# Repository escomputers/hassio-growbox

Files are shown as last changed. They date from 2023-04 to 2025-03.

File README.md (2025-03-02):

Home Assistant as growbox controller, using several different devices and sensors, connected via D1 Mini/ESP8266-12-e

## Home Assistant setup

### Install
1. Install Home Assistant as container (for Core installation check the "core" branch out)

```bash
docker compose up -d
```

2. Connect esp8266 to your PC using USB cable (buy one with serial converter integrated) and install ESPHome Device builder:

- https://esphome.io/guides/getting_started_command_line#bonus-esphome-device-builder
- https://esphome.io/guides/getting_started_hassio.html#installing-esphome-device-builder

3. Install the ESPHome integration

### Configure
[homeassistant-configuration directory](homeassistant-configuration/configuration.yaml) contains configuration for controlling USB relay board, using [RESTful Binary Sensor](https://www.home-assistant.io/integrations/binary_sensor.rest).\
To get it working, an API service must be started within raspbian OS and it allows you to install Home Assistant into a different host.\
Link to the repo: [usbAPI](https://github.com/escomputers/usbAPI)\
If you don't want to use a USB relay board, you could use a WIFI relay board like [this](https://denkovi.com/wifi-16-relay-board-modBus-tcp) and thus you can skip all the steps related to USB-API relay board management.

Here's the [example scripts.yaml file](homeassistant-configuration/scripts.yaml) containing the scripts used for controlling relay board via API

Here's the [example YAML](homeassistant-configuration/.storage/lovelace) for dashboard setup (cards and tiles)

## DEVICES

### Main controller
[D1 Mini](https://www.az-delivery.de/en/products/d1-mini) - [pinout](https://m.media-amazon.com/images/I/71b9yM7dFlL.jpg)\
[USB to serial converter](https://www.az-delivery.de/en/products/usb-auf-seriell-adapter-mit-ch340)

### Relay Board
[Denkovi USB 8 Channel](https://denkovi.com/usb-eight-channel-relay-board-for-automation) - [wiring](https://github.com/escomputers/hassio-growbox/blob/325ab9b5c127c14f19560fe0ca1c8efceda2f83e/wirings/12V-USB-8CH-relay-board-wiring.pdf)

| DEVICE | RPI4 |
| --- | --- |
| USB-B | USB |

### PWM Controller
[Universal AC MAINS Dimmer - MPDMv4.1](https://www.tindie.com/products/next_evo1/universal-ac-mains-dimmer-mpdmv41/)\
used for controlling 5 fans (4 oscillating + 1 inline)
| PWM board | ESP8266 |
| --- | --- |
| VCC | 3V3 |
| GND | GND |
| VCNT | GPIO15/D8 |

## Sensors
[D1-MINI/ESP8266 sensors wiring](https://github.com/escomputers/hassio-growbox/blob/325ab9b5c127c14f19560fe0ca1c8efceda2f83e/wirings/d1mini-esp8266-sensors-wiring.pdf)

[Best PINs to use on ESP8266](https://espeasy.readthedocs.io/en/latest/Reference/GPIO.html#best-pins-to-use-on-esp8266)

### Air
[BME280](https://www.adafruit.com/product/2652) Temperature + Humidity + Pressure (i2c bus)
| SENSOR | ESP8266 |
| --- | --- |
| VIN | 3V3 |
| GND | GND |
| SCK | SCL/GPIO5/D1 |
| SDO | SDA/GPIO4/D2 |

### Soil
[SHT20](https://www.makerfabs.com/soil-temperature-and-humidity-sensor-sht20.html) Temperature + Humidity (i2c bus)
| SENSOR | ESP8266 |
| --- | --- |
| RED | 3V3 |
| BLACK | GND |
| GREEN | SDA/GPIO4/D2 |
| YELLOW | SCL/GPIO5/D1 |

### CO2
[MH-Z19C NDIR](https://www.winsen-sensor.com/product/mh-z19c.html) (UART bus - 7pin terminal connection version)
| SENSOR | ESP8266 |
| --- | --- |
| PIN4 VIN | 5V |
| PIN3 GND | GND |
| PIN5 RX | TX/GPIO1/D10 |
| PIN6 TX | RX/GPIO3/D9 |

### Water Flow meter
[YF-S402B](https://robu.in/wp-content/uploads/2021/07/NB178.pdf)

WARNING: enable option "Allow the device to perform Home Assistant actions" in Settings/Devices&Services/ESPHome/configure

<ins>Installation</ins>

- Straight Pipe Section Before and After the Sensor

  - Upstream (Inlet):
  Ensure there is a sufficient length of straight pipe (typically 10–15 times the pipe diameter) before the sensor. This helps in creating a uniform, laminar flow profile and minimizes turbulence before the water reaches the sensor.

  - Downstream (Outlet):
  Similarly, maintain a straight run after the sensor (at least 5–10 pipe diameters) if possible. This prevents any backflow or turbulent eddies from affecting the sensor’s operation.

- Avoid installing the sensor in positions where gravity or buoyancy effects could cause bubbles or sediment accumulation.

- Avoiding Vibrations and Mechanical Interference

  - Mount the sensor securely using proper fittings to prevent vibrations. Excessive vibration can introduce noise into the measurement. Ensure that the sensor is not subjected to mechanical stress or movement, as this can affect the pulse signal.

- Minimize Air Entrapment and Bubbles

  - Install the sensor in a part of the piping system where air is unlikely to be trapped. Air bubbles can cause the turbine to rotate erratically, leading to inaccurate readings.

- Stable Electrical Connections

  - Use good quality wiring and, if possible, shielded cables to reduce electrical noise, which might cause false triggering or counting errors.
  Enable the internal pull-up resistor to maintain a stable digital signal.

| YF-S402B | ESP8266 |
| --- | --- |
| RED | 5V |
| BLACK | GND |
| YELLOW | GPIO12/D6  |

<ins>Calculate calibration constant</ins>

1. Measure the quantity of water running through the sensor in a specific time interval

2. Count the pulses over time to calculate the exact flow rate frequency

3. Adjust the default calibration constant based on observed data to improve precision

For example:\
If you collected 1,6 liters in 60 seconds:\
Flow Rate (Q) = 1,6 Liters per minute

Calibration Constant (K) = Pulses/minute (P) : Flow Rate (Q)\
1.596,35635625 = 2.554,17017 (median of all pulses measurements) : 1,6

Volume (L) = Pulses : K\
1,6 = 2.554,17017 : 1.596,35635625

## POWER

| DEVICE | REQUIRED POWER SOURCES |
| --- | --- |
| Denkovi USB 8CH relay board | 12V 1A + 220V|
| Esp8266 | 5V/3.3V 1A |
| Raspberry Pi 4 | 5V 2A|
| Raspberry Pi 4 Fan | 9V 1A|
| Power sockets | 220V 16A (1,5mm<sup>2</sup> cables)|

## 3D CASES

Take a look at [3D directory](3D/)\
References:
- Raspberry Pi 4 case (40mm fan) by John_Sinclair on [Thingiverse](https://www.thingiverse.com/thing:3723481)
- 12V USB 8 Channel relay board by polysquare on [Thingverse](https://www.thingiverse.com/thing:2306082)
- BME280 case by leptitnicolas on [Thingverse](https://www.thingiverse.com/thing:3809818)
- Arduino nano + 2 channel arduino relay + voltage stepdown box by flying_ginger on [Thingverse](https://www.thingiverse.com/thing:3162083). Used for housing ESP8266 (by making a drawer/slot manually since screw holes aren't available on the board), MH-Z19, cables and as attach surface for placing BME280 externally.

---

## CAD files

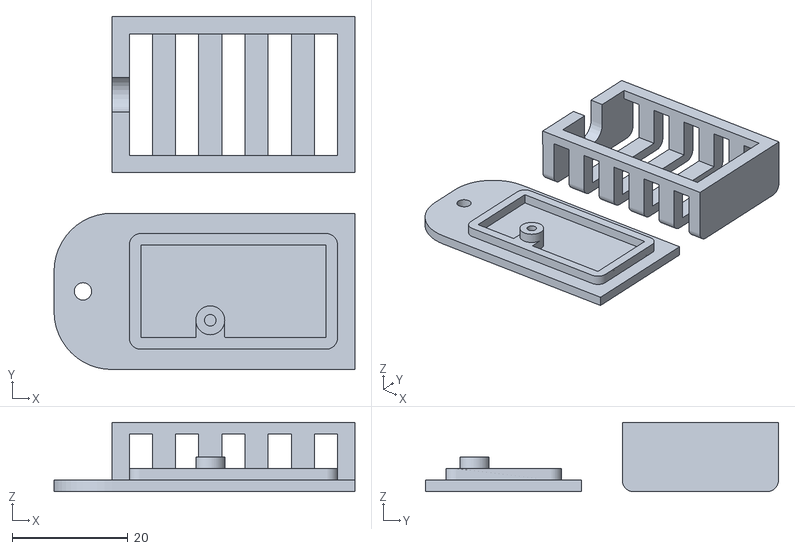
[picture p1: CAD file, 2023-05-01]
3D/bme280/BME280BoxV6.stl
52.0 x 61.0 x 12.0

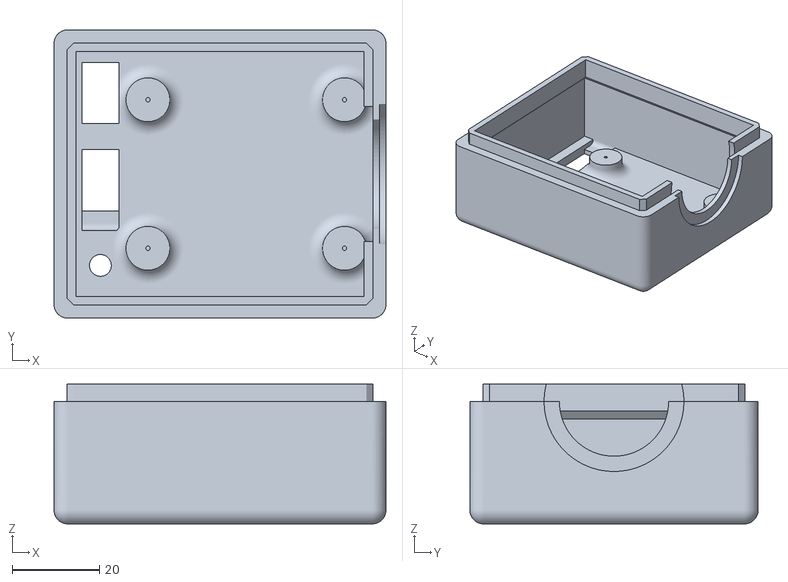
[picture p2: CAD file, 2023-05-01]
3D/esp/arduino_box_top.stl
76.0 x 66.0 x 32.0

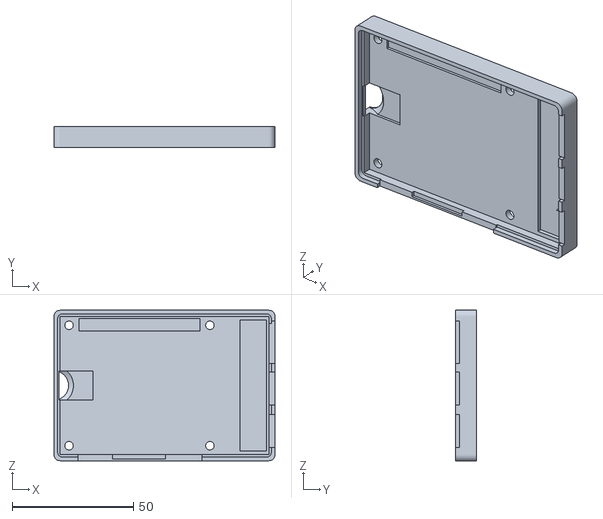
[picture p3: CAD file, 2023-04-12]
3D/raspberry-pi/lower.stl
91.0 x 8.50 x 62.0

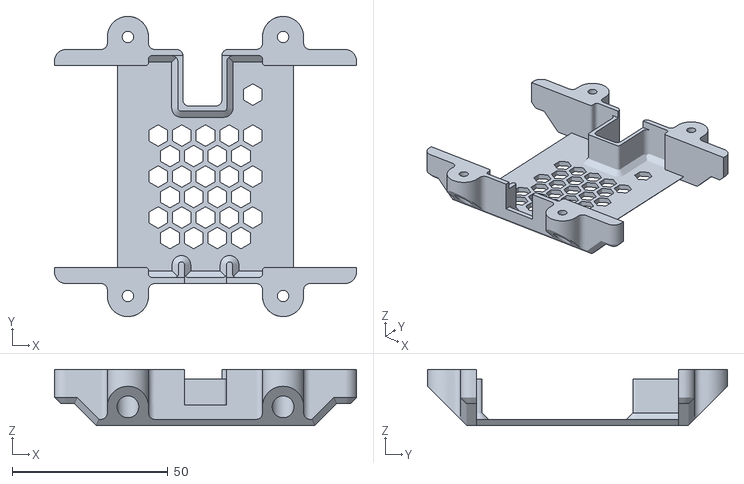
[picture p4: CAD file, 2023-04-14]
3D/usb-8ch-relay-board/Top.stl
97.0 x 96.4 x 18.0

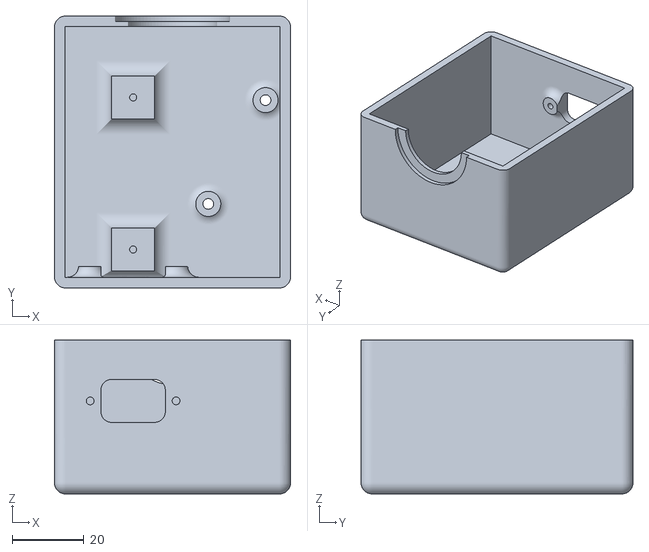
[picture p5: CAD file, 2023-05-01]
3D/esp/arduino_box_bottom.stl
66.0 x 76.0 x 43.0

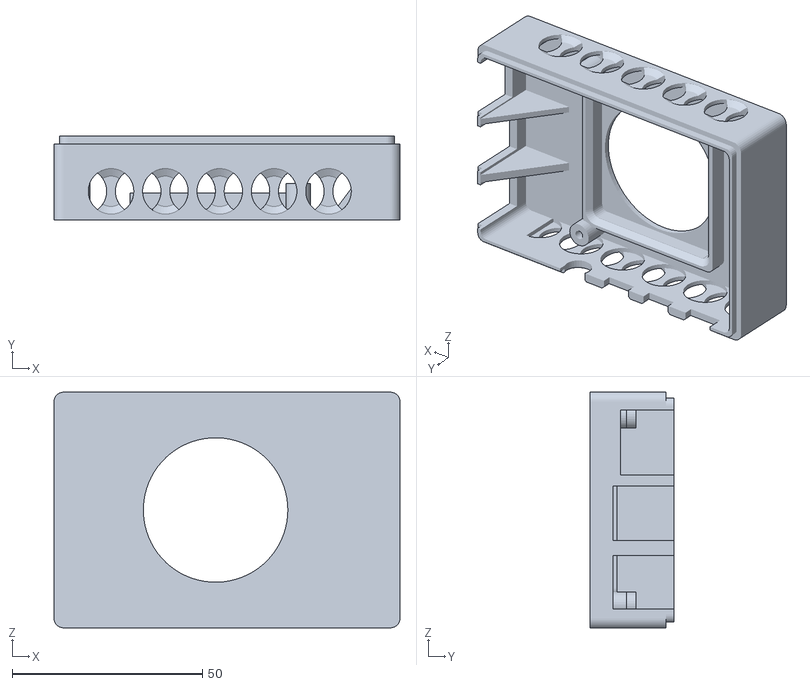
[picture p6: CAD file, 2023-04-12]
3D/raspberry-pi/upper.stl
91.0 x 22.0 x 62.0

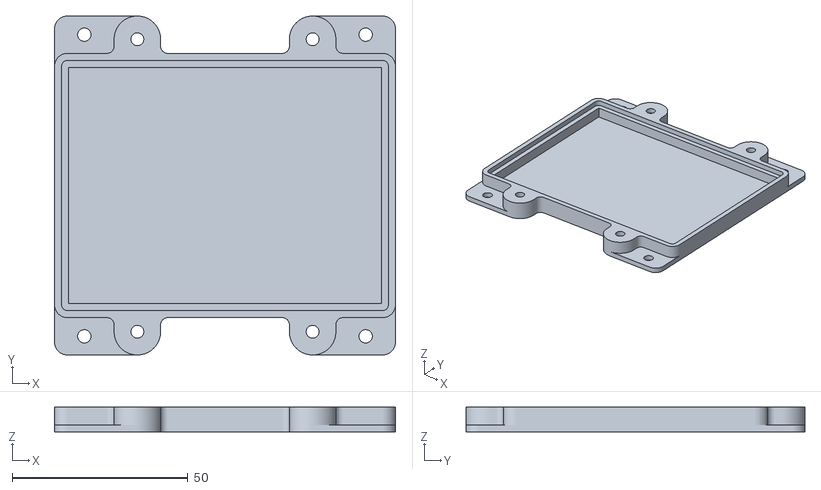
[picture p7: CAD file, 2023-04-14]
3D/usb-8ch-relay-board/Base.stl
97.0 x 96.4 x 7.00

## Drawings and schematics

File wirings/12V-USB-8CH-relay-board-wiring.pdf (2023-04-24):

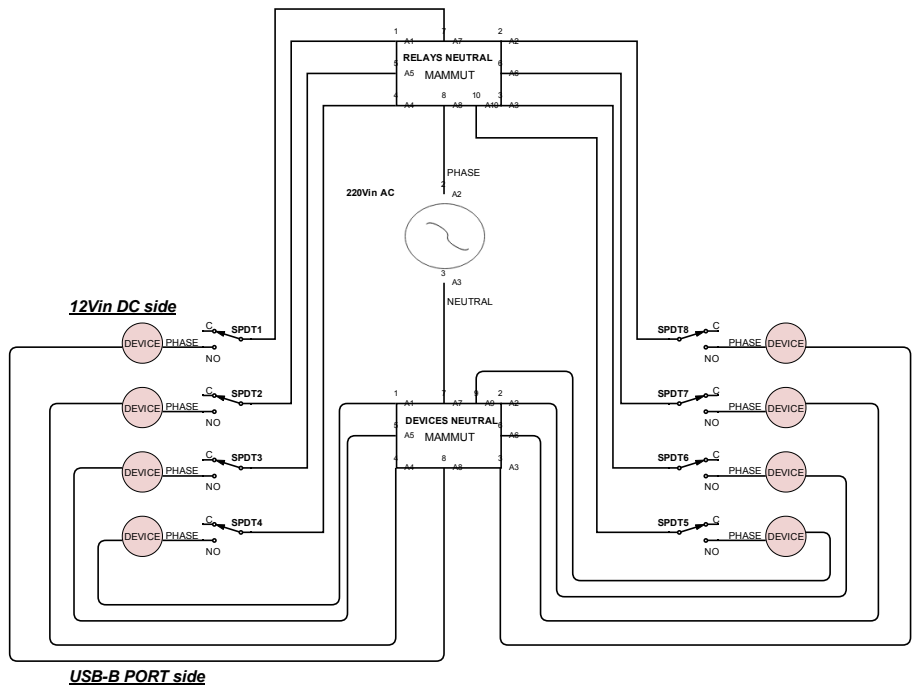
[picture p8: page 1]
SPDT1; SPDT2; SPDT3; SPDT4; SPDT5; SPDT6; SPDT7; SPDT8; DEVICE PHASE; DEVICE; PHASE; PHASE DEVICE; 12Vin DC side; MAMMUT; DEVICES NEUTRAL; 220Vin AC; NEUTRAL

RELAYS NEUTRAL 5 A5 MAMMUT | 8 10 | 6 A6

USB-B PORT side

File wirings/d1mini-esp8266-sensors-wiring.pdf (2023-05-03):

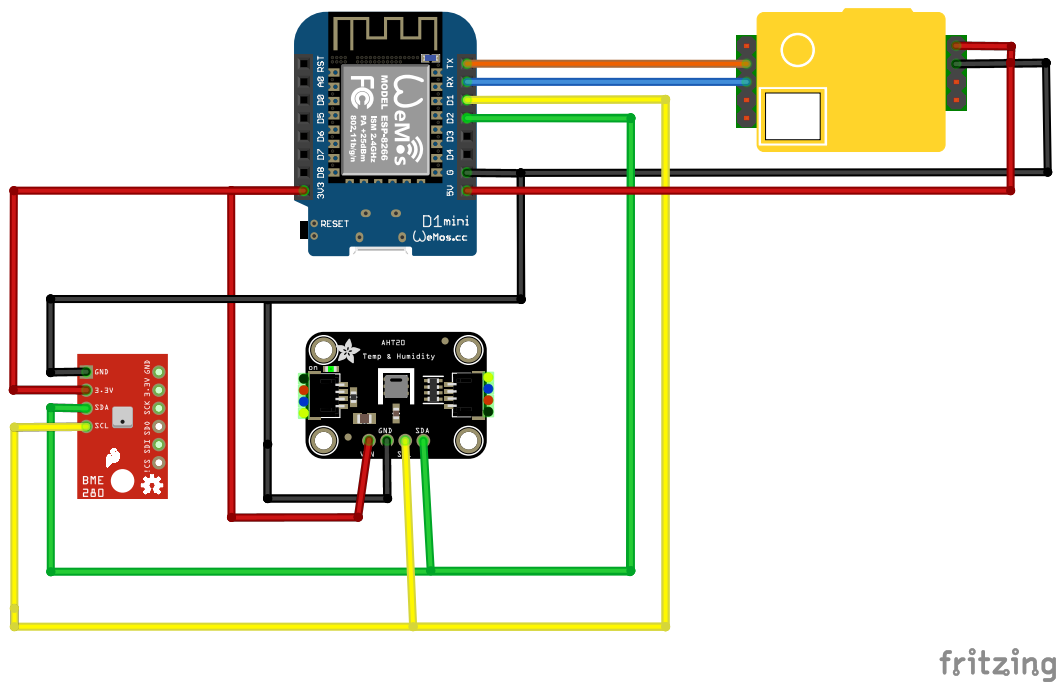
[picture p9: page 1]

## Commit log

2023-03-26 added bme280 humidity and pressure
2023-03-27 threadManager converted in bash
2023-03-27 changed env variable import due to threadsManager.sh
2023-03-30 changed sensor threads logic
2023-04-03 added esphome config for mh-z19 sensor
2023-04-04 added bme280 and sht20 sensor to esphome
2023-04-12 added first stl files for rpi case
    [lower.stl, upper.stl]
2023-04-14 added STL for usb relay board
    [Base.stl, Top.stl, lower.stl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]
2023-04-24 added 8CH USB relay board wiring
2023-04-24 added ref to usb board wiring
2023-05-01 added HA config for REST sensors + latest snapshot
2023-05-01 repo re-org + updated README + added .stl files
    [BME280BoxV6.stl, arduino_box_bottom.stl, arduino_box_top.stl]
2023-05-03 added esp8266 wiring
2024-04-25 Added pwm output
2024-04-28 Added PWM + updated documentation + removed useless files
2025-02-19 Water flow meter integration (#3)
    * Adding water flow meter
    * Update README.md
    * Update README.md
    * Adding config for water flow counters
    * Stable integration of water flow sensor
